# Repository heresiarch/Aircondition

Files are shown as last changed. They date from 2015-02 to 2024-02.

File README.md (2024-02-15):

# Aircondition
A Project using TX21IT+ wireless 868Mhz sensors with RFM12 and PIC24F to control air ventilators based on absolute humidity.
You will find the whole C source and Eagle project files inside.
The Circuit and Software uses the following technologies:
* OW protocoll managing config data for DS2430A 1 wire 256 EEPROM
* Microchip MCU PIC24F P24FJ32GB002
* Hope RFM12B IRQ driven communication with TX21IT+ LaCrosse IT+ Weather sensors
* IC2 communication with Newhaven LCD Display NHD-C0216CiZ-FN-FBW-3V (which was tricky)
* Rotary encoder using digital filter algorithm for debouncing for configuring the system  

The setup is very simple:  
0. The system checks for valid config and CRC in the EEPROM and if OK goes to 3 or step 1  
1. You have to register the 2 TX21IT+ sensors each time you change their battery the get a new ID.  
2. Then you setup in sensor, out sensor, absolute humidity threshold, pause time, run time for ventitalors which is stored in the OW EEPROM  
3. Then the mainloop starts  
3.1. In the Mainlopp the MCU will listen with the RFM12B for 30 TX21IT+ records  
3.2. The ID of the records is used to match in and out sensors configured in step 1 and 2, if no sensor matches found it starts @1   
3.3 The temperature and relative humidity will be used to calculate absolute humidity for the in and out sensor  
3.5 If abs-hum-in > (threshold + abs-hum-out) the AC ventilators will be switched with an SCR  will run as long the configured runtime in step 2  
3.6. The system waits until the pause time is over and starte @3  
At any time a long press on the rotary knob will start reconfiguring mode step 1  

The system runs rockstable since 10 years in my garage with Marley Silenzio Ventilators.  
Not shown is the snubber circuit using a TVS, X2 capacitor and an high voltage resistor to reduce spikes to protect the SCR.
Bottom ventilator blows air from outside, top ventilator blows air to outside.
No moldy smell and always uses the right time for air condition to prevent mold creation during all seasons.  
The project uses MPLABX and has also a .project Eclipse file which I used to utilize Git Eclipse integration to manage versioning.

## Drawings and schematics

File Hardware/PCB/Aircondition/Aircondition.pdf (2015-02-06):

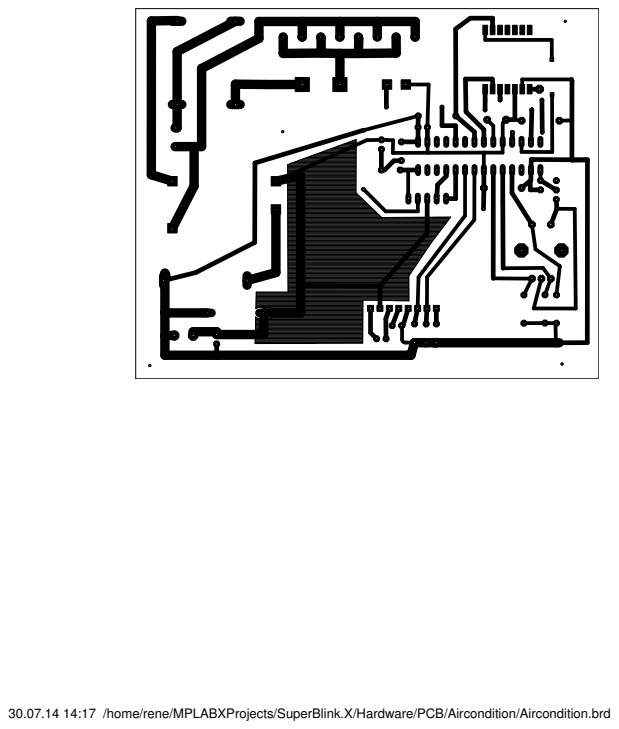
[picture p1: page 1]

30.07.14 14:17 /home/rene/MPLABXProjects/SuperBlink.X/Hardware/PCB/Aircondition/Aircondition.brd

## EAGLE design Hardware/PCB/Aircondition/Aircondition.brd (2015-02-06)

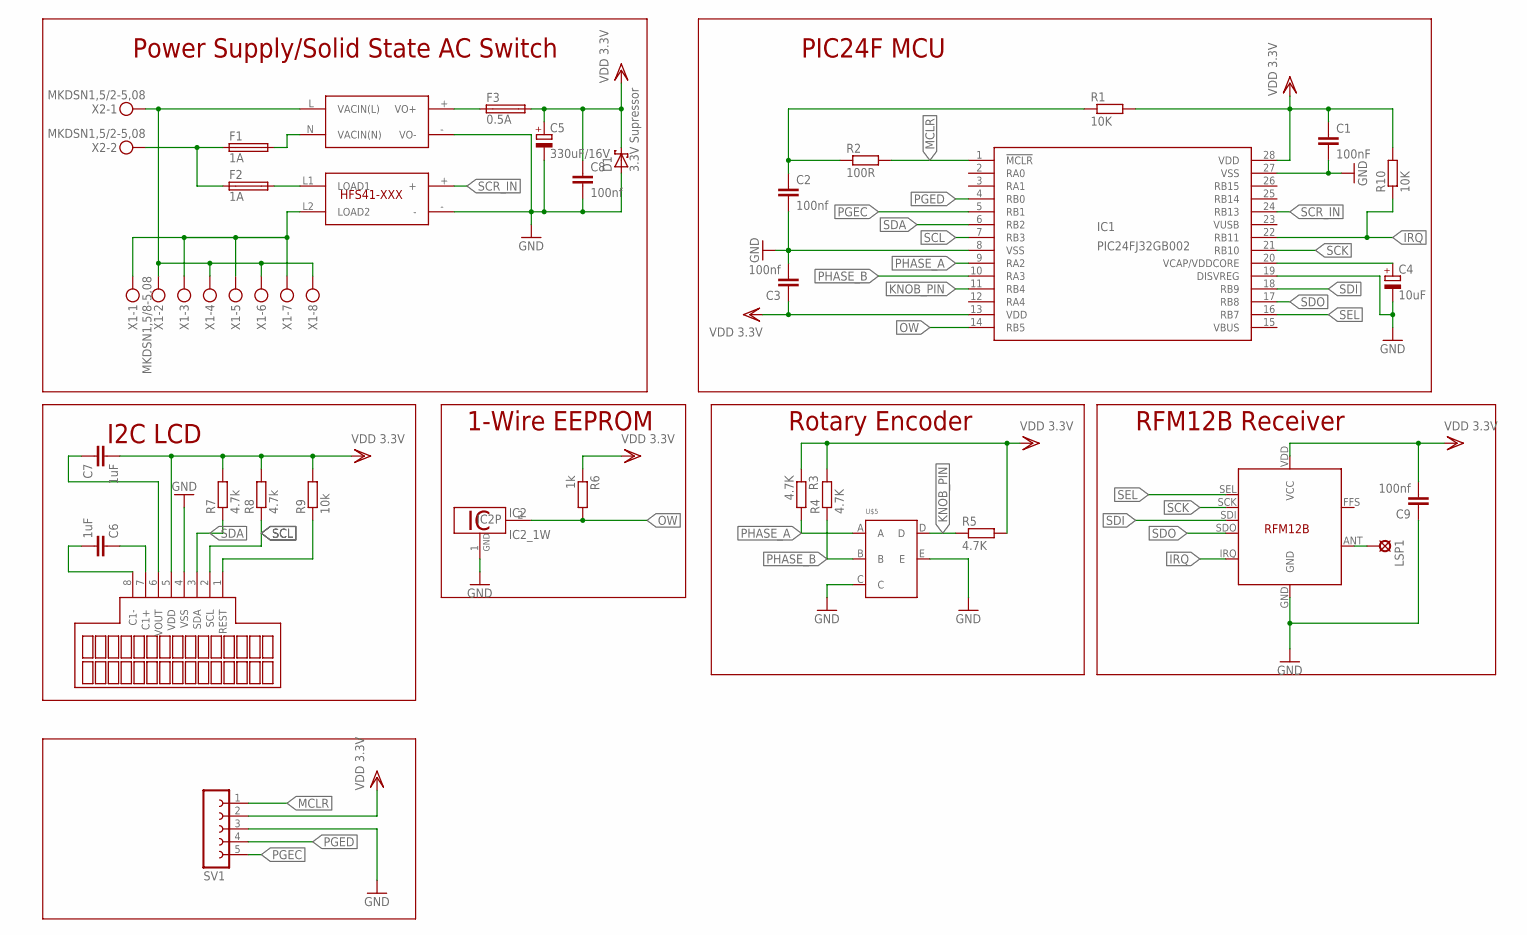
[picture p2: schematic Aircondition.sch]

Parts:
C1: 100nF; C025-025X050
C2, C8: 100nf; C025-025X050
C3, C9: 100nf; C102-043X133
C4: 10uF; E5-5
C5: 330uF/16V; E5-10,5
C6, C7: 1uF; C025-025X050
D1: 3.3V Supressor; C4111-15
F1, F2: 1A; SH22,5A
F3: 0.5A; SH22,5A
IC1: PIC24FJ32GB002; DIL28-3
IC2: DS2431; TO92-
LSP1: ANT; LSP10
R1: 10K; 0204/5
R2: 100R; 0204/5
R3, R4, R5: 4.7K; 0204/7
R6: 1k; 0207/2V
R7, R8: 4.7k; 0204/5
R9: 10k; 0204/5
R10: 10K; 0207/10
SV1: FE05-1
U$1: RAC01-3.3SC; RAC01-XXSC
U$2: HFS41D-240A5Z-NGSTANDARD; HFS41-EXPOXY-RESIN
U$3: NHD-C0216CIZ-FN-FBW-3VSIL8-2.54; SIL8-2.54
U$4: RFM12B
U$5: ENCODER-E; ENCODER
X1: MKDSN1,5/8-5,08
X2: MKDSN1,5/2-5,08

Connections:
GND: C1.2, C2.2, C3.2, C4.-, C5.-, C8.2, C9.1, D1.A, IC1.8 (VSS), IC1.19 (DISVREG), IC1.27 (VSS), IC2.1 (GND), SV1.3, U$1.- (VO-), U$2.-, U$3.4 (VSS), U$4.GND, U$5.C, U$5.E
IRQ: IC1.22 (RB11), R10.1, U$4.IRQ
KNOB_PIN: IC1.11 (RB4), R5.1, U$5.D
MCLR: IC1.1 (!MCLR), R2.2, SV1.1
unnamed: F1.2, U$1.N (VACIN(N))
unnamed: F2.2, U$2.L1 (LOAD1)
unnamed: F1.1, F2.1, X2.2
unnamed: U$2.L2 (LOAD2), X1.1, X1.3, X1.5, X1.7
unnamed: C2.1, R1.1, R2.1
unnamed: U$1.L (VACIN(L)), X1.2, X1.4, X1.6, X1.8, X2.1
unnamed: F3.1, U$1.+ (VO+)
unnamed: C4.+, IC1.20 (VCAP/VDDCORE)
unnamed: LSP1.MP, U$4.ANT
unnamed: C6.2, U$3.8 (C1-)
unnamed: C6.1, U$3.7 (C1+)
unnamed: C7.1, U$3.6 (VOUT)
unnamed: R9.1, U$3.1 (REST)
OW: IC1.14 (RB5), IC2.2 (1W), R6.2
PGEC: IC1.5 (RB1), SV1.5
PGED: IC1.4 (RB0), SV1.4
PHASE_A: IC1.9 (RA2), R3.2, U$5.A
PHASE_B: IC1.10 (RA3), R4.1, U$5.B
SCK: IC1.21 (RB10), U$4.SCK
SCL: IC1.7 (RB3), R8.1, U$3.2 (SCL)
SCR_IN: IC1.24 (RB13), U$2.+
SDA: IC1.6 (RB2), R7.1, U$3.3 (SDA)
SDI: IC1.18 (RB9), U$4.SDI
SDO: IC1.17 (RB8), U$4.SDO
SEL: IC1.16 (RB7), U$4.SEL
VDD: C1.1, C3.1, C5.+, C7.2, C8.1, C9.2, D1.C, F3.2, IC1.13 (VDD), IC1.28 (VDD), R1.2, R3.1, R4.2, R5.2, R6.1, R7.2, R8.2, R9.2, R10.2, SV1.2, U$3.5 (VDD), U$4.VDD (VCC)

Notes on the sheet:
Power Supply/Solid State AC Switch
I2C LCD
1-Wire EEPROM
Rotary Encoder
PIC24F MCU
RFM12B Receiver

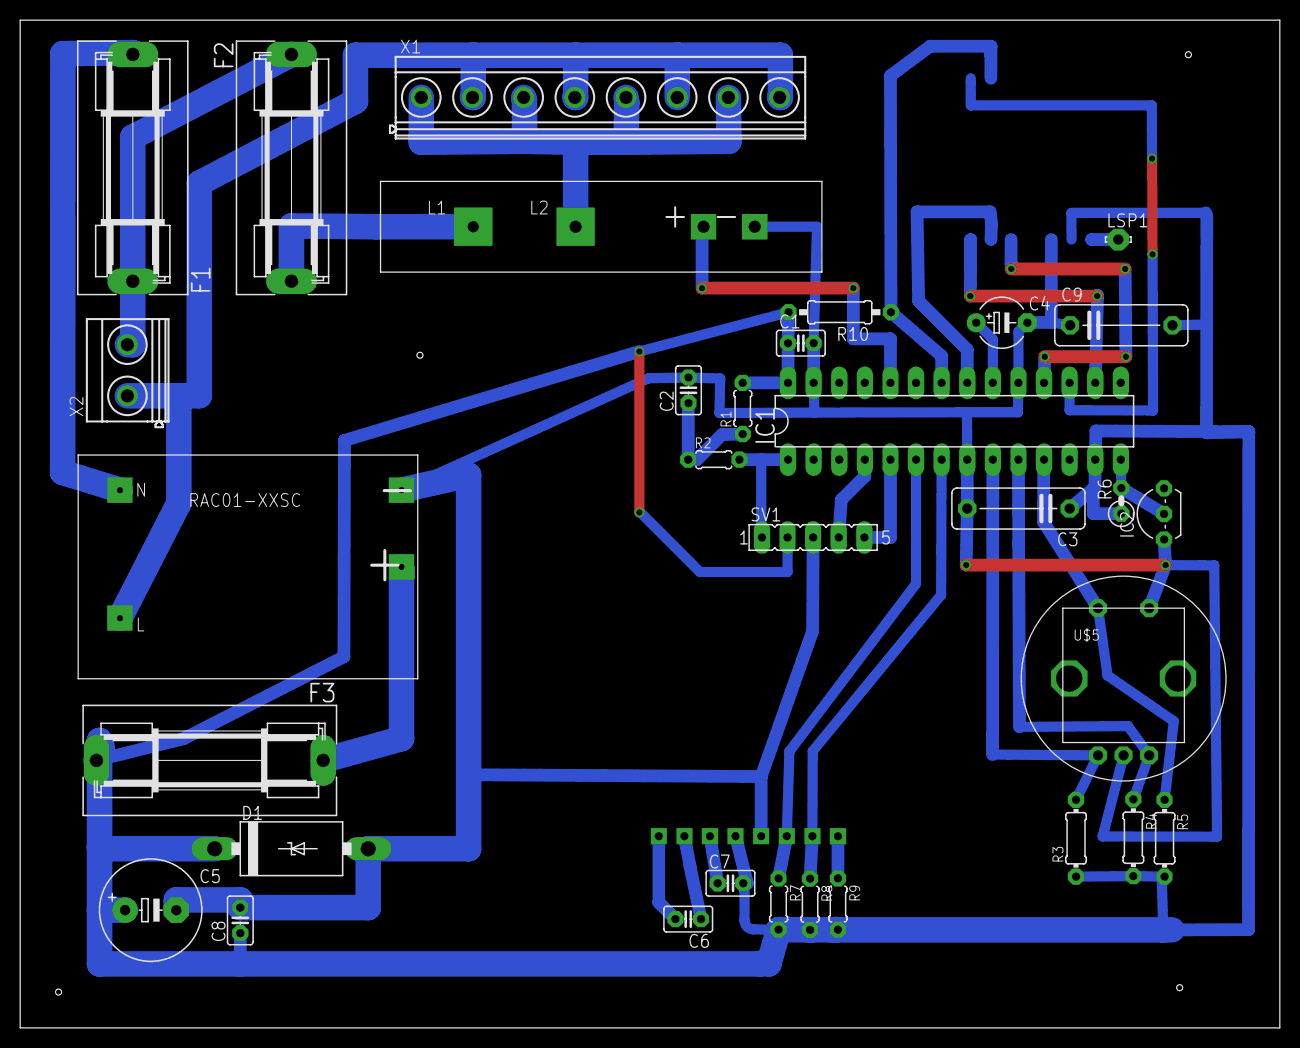
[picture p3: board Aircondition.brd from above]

Board: 2 copper layers, 125.0 x 100.0 mm, 34 parts (1 on the bottom side), 30 nets.

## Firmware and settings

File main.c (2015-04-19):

/* 
 * File:   main.c
 * Author: rene
 *
 * Created on 18. August 2013, 12:57
 */


#include <string.h>
#include <stdint.h>
#include <xc.h>
//#include <p24FJ32GB002.h>
#define FCY 8000000UL
#include <libpic30.h>
#include "LCD_I2C_ST7032i.h"
#include "RFM12B.h"
#include "TX21IT.h"
#include "LCD_I2C_ST7032i.h"
#include "1wire.h"
#include "rotary_encoder.h"
#include "stringconversion.h"
#include "aircondition.h"

/*
// http://www.microchip.com/forums/tm.aspx?m=491233
_CONFIG1(JTAGEN_OFF & GCP_OFF & GWRP_OFF & ICS_PGx1 & FWDTEN_OFF & WINDIS_OFF & FWPSA_PR32 & WDTPS_PS8192);
_CONFIG2(IESO_OFF & FNOSC_FRCPLL & OSCIOFNC_ON & POSCMOD_NONE & PLL96MHZ_ON & PLLDIV_DIV2 & FCKSM_CSDCMD & IOL1WAY_OFF);
_CONFIG3(WPFP_WPFP0 & SOSCSEL_IO & WUTSEL_FST & WPDIS_WPDIS & WPCFG_WPCFGDIS & WPEND_WPENDMEM)
_CONFIG4(DSWDTPS_DSWDTPS3 & DSWDTOSC_LPRC & RTCOSC_LPRC & DSBOREN_OFF & DSWDTEN_OFF)
*/


// CONFIG4
#pragma config DSWDTPS = DSWDTPS3       // DSWDT Postscale Select (1:128 (132 ms))
#pragma config DSWDTOSC = LPRC          // Deep Sleep Watchdog Timer Oscillator Select (DSWDT uses Low Power RC Oscillator (LPRC))
#pragma config RTCOSC = LPRC            // RTCC Reference Oscillator Select (RTCC uses Low Power RC Oscillator (LPRC))
#pragma config DSBOREN = OFF            // Deep Sleep BOR Enable bit (BOR disabled in Deep Sleep)
#pragma config DSWDTEN = OFF            // Deep Sleep Watchdog Timer (DSWDT disabled)

// CONFIG3
#pragma config WPFP = WPFP0             // Write Protection Flash Page Segment Boundary (Page 0 (0x0))
#pragma config SOSCSEL = IO             // Secondary Oscillator Pin Mode Select (SOSC pins have digital I/O functions (RA4, RB4))
#pragma config WUTSEL = FST             // Voltage Regulator Wake-up Time Select (Fast regulator start-up time used)
#pragma config WPDIS = WPDIS            // Segment Write Protection Disable (Segmented code protection disabled)
#pragma config WPCFG = WPCFGDIS         // Write Protect Configuration Page Select (Last page and Flash Configuration words are unprotected)
#pragma config WPEND = WPENDMEM         // Segment Write Protection End Page Select (Write Protect from WPFP to the last page of memory)

// CONFIG2
#pragma config POSCMOD = NONE           // Primary Oscillator Select (Primary Oscillator disabled)
#pragma config I2C1SEL = PRI            // I2C1 Pin Select bit (Use default SCL1/SDA1 pins for I2C1 )
#pragma config IOL1WAY = OFF            // IOLOCK One-Way Set Enable (The IOLOCK bit can be set and cleared using the unlock sequence)
#pragma config OSCIOFNC = ON            // OSCO Pin Configuration (OSCO pin functions as port I/O (RA3))
#pragma config FCKSM = CSDCMD           // Clock Switching and Fail-Safe Clock Monitor (Sw Disabled, Mon Disabled)
#pragma config FNOSC = FRCPLL           // Initial Oscillator Select (Fast RC Oscillator with Postscaler and PLL module (FRCPLL))
#pragma config PLL96MHZ = ON            // 96MHz PLL Startup Select (96 MHz PLL Startup is enabled automatically on start-up)
#pragma config PLLDIV = DIV2            // USB 96 MHz PLL Prescaler Select (Oscillator input divided by 2 (8 MHz input))
#pragma config IESO = OFF               // Internal External Switchover (IESO mode (Two-Speed Start-up) disabled)

// CONFIG1
#pragma config WDTPS = PS8192           // Watchdog Timer Postscaler (1:8,192)
#pragma config FWPSA = PR32             // WDT Prescaler (Prescaler ratio of 1:32)
#pragma config WINDIS = OFF             // Windowed WDT (Standard Watchdog Timer enabled,(Windowed-mode is disabled))
#pragma config FWDTEN = OFF             // Watchdog Timer (Watchdog Timer is disabled)
#pragma config ICS = PGx1               // Emulator Pin Placement Select bits (Emulator functions are shared with PGEC1/PGED1)
#pragma config GWRP = OFF               // General Segment Write Protect (Writes to program memory are allowed)
#pragma config GCP = OFF                // General Segment Code Protect (Code protection is disabled)
#pragma config JTAGEN = OFF             // JTAG Port Enable (JTAG port is disabled)


#define OUTPUTBUFSIZE 16
char outbuf1[OUTPUTBUFSIZE];
char outbuf2[OUTPUTBUFSIZE];
#define RECEIVEBUFSIZE 5
char receiveBuff[RECEIVEBUFSIZE];

volatile uint8_t byteCount = 0;

#define RELAIS_OUT_PIN LATBbits.LATB13
#define RELAIS_OUT_DIR TRISBbits.TRISB13

#define GLOBAL_BUFFER_ELEMENTS 30
TX21SensorData global_buffer[GLOBAL_BUFFER_ELEMENTS];
volatile uint16_t global_counter = 0;


enum Status
{
	CHECK_CONFIG = 1, SET_CONFIG, RUN, ERROR
};

typedef enum Status StatusEnum;
StatusEnum s = CHECK_CONFIG;
StatusEnum old = ERROR;
volatile char dirty = 0;

AirConfigData configData = {0};

// functions for state machine
void state_check_config(void);
void state_set_config(void);
void state_run(void);

int findSensors(void);
uint8_t chooseSensorID(char* msg, TX21SensorData* outArray, uint8_t size);
int16_t chooseIntVal(char* msg, int16_t min, int16_t max, int16_t step);
float chooseFloatVal(char* msg, float min, float max, float step,float precision);


void enableRFM12(void);
void resetRFM12(void);

void Timer1Init(void);

int main(int argc, char** argv) {

    global_counter = 0;

    CLKDIVbits.PLLEN       = 1;     //PLL enable
    while(OSCCONbits.LOCK!=1) {};   //wait for stable PLL
    __delay_ms(5000);

    AD1PCFGL = 0xFFFF;      // all Ports digital
    TRISBbits.TRISB15 = 0;
    TRISBbits.TRISB14 = 0;
    TRISBbits.TRISB13 = 0;
    //RESET Line of RFM12b
    TRISBbits.TRISB11 = 1;
    //KNOB_PIN
    TRISBbits.TRISB4 = 1;
    //Rotary Phases
    TRISAbits.TRISA2 = 1;
    TRISAbits.TRISA4 = 1;

    RPINR0	=	0x0B00;	//set RP11 to external interrupt 1
    INTCON2 = 0xFFFF;   /*Setup INT0, INT1, INT2, interupt on falling edge*/
    IFS1bits.INT1IF = 0;    /*Reset INT1 interrupt flag */
    IEC1bits.INT1IE = 1;    /*Enable INT1 Interrupt Service Routine */
    IPC5bits.INT1IP = 5;	/*set low priority*/

    //RELAIS
    RELAIS_OUT_DIR = 0;
    RELAIS_OUT_PIN = 0;
    Timer1Init();
    lcd2_init();
    encode_init();
    s = SET_CONFIG;
    old = ERROR;
    lcd2_clear();
    lcd2_home();
    lcd2_write_str_xy(0,0,"Aircondition");
    lcd2_write_str_xy(0,1,"Rene Meyer 2014");
    __delay_ms(5000);
    s = CHECK_CONFIG;
    while(1)
    {
        // State changed
	if(old != s)
	{
            lcd2_clear();
            lcd2_home();
            old = s;
            dirty = 1;	
	}
        switch (s)
	{
		case CHECK_CONFIG:
			state_check_config();
		break;
                case SET_CONFIG:
			state_set_config();
		break;
                case RUN:
                        state_run();
		break;
                case ERROR:
			state_set_config();
		break;
	}

    }

    return 0;
}

void state_check_config(void)
{
    // first read configdata
    uint8_t len = sizeof(AirConfigData);
    read_ds2430(6, (uint8_t*)&configData, len);
    // read crc
    uint8_t crc = 0;
    read_ds2430(6+len, (uint8_t*)&crc, sizeof(uint8_t));
    uint8_t realcrc = crc8((uint8_t*)&configData,len);
    lcd2_clear();
    lcd2_home();
    if(crc != realcrc)
    {
        lcd2_write_str_xy(0,0,"Invalid Config");
        lcd2_write_str_xy(0,1,"Press Knob");
        while(!knob_up());
        s = SET_CONFIG;
    }
    else
    {
        lcd2_write_str_xy(0,0,"Config OK");
        __delay_ms(1000);
        s = RUN;
    }
}

void state_set_config(void)
{
    uint16_t found = findSensors();
    if(found == 0)
    {
        lcd2_clear();
        lcd2_home();
        lcd2_write_str_xy(0,0,"No Sensors found!");
        lcd2_write_str_xy(0,1,"Restart Config");
        while(!knob_up());
        s = CHECK_CONFIG;
    }
    else
    {
        configData.inSensorID = chooseSensorID("Choose In Sensor", global_buffer, found);
        configData.outSensorID = chooseSensorID("Choose Out Sensor", global_buffer, found);
        configData.runTime = chooseIntVal("Runtime min",MIN_RUN_MINUTES,MAX_RUN_MINUTES,RUN_STEP);
        configData.pauseTime = chooseIntVal("Pause min",MIN_PAUSE_TIME_MINUTES, MAX_PAUSE_TIME_MINUTES,PAUSE_TIME_MINUTES_STEP);
        configData.breakAfterRunTime = chooseIntVal("Break min", MIN_BREAK_BTW_RUNS_MINUTES, MAX_BREAK_BTW_RUNS_MINUTES,BREAK_BTW_RUNS_MINUTES_STEP);
        configData.threshold = chooseFloatVal("Ta Thresh. g/m^3",MIN_ABS_HUMIDITY_THRESHOLD, MAX_ABS_HUMIDITY_THRESHOLD, ABS_HUMIDITY_STEP,ABS_HUMIDITY_PRECISION);
        //Write Config to EEPROM
        uint8_t len = sizeof(AirConfigData);
        uint8_t buf[len];
        memcpy(buf,&configData,len);
        write_ds2430(6, buf, len);
        //write crc to EEPROM
        uint8_t crc = crc8((uint8_t*)&configData,len);
        uint8_t buf2[2];
        buf2[0]=crc;
        buf2[1]=0;
        write_ds2430(6+len, buf2, sizeof(uint8_t));
        lcd2_clear();
        lcd2_home();
        lcd2_write_str_xy(0,0,"Config. written");
        lcd2_write_str_xy(0,1,"Press Knob ");
        while(!knob_up());
        s = CHECK_CONFIG;
    }

}

void state_run(void)
{
    TX21SensorData inData;
    TX21SensorData outData;
    while(s == RUN)
    {
        char out = 0;
        int pause_counter = 0;
        int break_counter = 0;
        int out_counter = 0;
        int found = findSensors();
        if(found <= 0)
        {
            lcd2_clear();
            lcd2_home();
            lcd2_write_str_xy(0,0,"Error:");
            lcd2_write_str_xy(0,0,"No Sensors!");
            while(!knob_up());
            s = ERROR;    
            return;
        }
        int inIdx = -1;
        int outIdx = -1;
        int i;
        for(i = 0; i < found; i++)
        {
            if(global_buffer[i].sensorID == configData.inSensorID)
            {
                inIdx = i;
            }
            else if(global_buffer[i].sensorID == configData.outSensorID)
            {
                outIdx = i;
            }
        }
        if(inIdx < 0 || outIdx < 0)
        {
            lcd2_clear();
            lcd2_home();
            lcd2_write_str_xy(0,0,"Error:");
            lcd2_write_str_xy(0,1,"No ID Match!");
            while(!knob_up());
            s = ERROR;
            return;
        }
        inData = global_buffer[inIdx];
        outData = global_buffer[outIdx];
        float absHumIn = getAbsoluteHumidity(&inData);
        float absHumOut = getAbsoluteHumidity(&outData);
        float comp = absHumOut + configData.threshold;
        if(comp < absHumIn)
        {
            out = 1;
            RELAIS_OUT_PIN = 1;
        }
        else
        {
            out = 0;
            RELAIS_OUT_PIN = 0;
        }
        //loop for Running Aircondition
        while((out_counter < configData.runTime * 60) && out && s == RUN)
        {
            char battbuff[8];
            lcd2_clear();
            lcd2_home();
            lcd2_write_str_xy(0,0,"Air Condition");
            lcd2_write_str_xy(0,1,"Run ");
            int secsLeft = (configData.runTime * 60 - out_counter);
            lcd2_write_U16(secsLeft,0);
            lcd2_write_str(" sec");
            __delay_ms(2000);
            lcd2_clear();
            lcd2_home();
            lcd2_write_str("In:");
            lcd2_write_U8_hex(inData.sensorID);
            lcd2_write_str(" ");
            getSensorBatteryStateString(battbuff,sizeof(battbuff),&inData);
            lcd2_write_str(battbuff);
            getSensorValueString(outbuf1,OUTPUTBUFSIZE, &inData);
            lcd2_write_str_xy(0,1,outbuf1);
            __delay_ms(2000);
            lcd2_clear();
            lcd2_home();
            lcd2_write_str("Out:");
            lcd2_write_U8_hex(outData.sensorID);
            lcd2_write_str(" ");
            getSensorBatteryStateString(battbuff,sizeof(battbuff),&outData);
            lcd2_write_str(battbuff);
            getSensorValueString(outbuf1,OUTPUTBUFSIZE, &outData);
            lcd2_write_str_xy(0,1,outbuf1);
            __delay_ms(2000);
            out_counter+=6;
            if(long_pressed())
            {
                s = ERROR;
            }
        }
        // special wait after run
        if(out == 1)
        {
            out = 0;
            RELAIS_OUT_PIN = 0;
            while(break_counter < configData.breakAfterRunTime * 60)
            {
                lcd2_clear();
                lcd2_home();
                lcd2_write_str_xy(0,0,"Air Condition");
                lcd2_write_str_xy(0,1,"Break after Run ");
                int secsLeft = (configData.breakAfterRunTime * 60 - break_counter);
                lcd2_write_U16(secsLeft,0);
                lcd2_write_str(" sec");
                __delay_ms(1000);
                break_counter += 1;
                if(long_pressed())
                {
                    s = ERROR;
                }
            }
        }
        
        while(pause_counter < configData.pauseTime * 60 && s == RUN)
        {
            lcd2_clear();
            lcd2_home();
            lcd2_write_str_xy(0,0,"Air Condition");
            lcd2_write_str_xy(0,1,"Pause ");
            int secsLeft = (configData.pauseTime * 60 - pause_counter);
            lcd2_write_U16(secsLeft,0);
            lcd2_write_str(" sec");
            __delay_ms(1000);
            pause_counter += 1;
            if(long_pressed())
            {
                s = ERROR;
            }
        }
    }
}


int findSensors()
{
    global_counter = 0;
    lcd2_clear();
    lcd2_home();
    lcd2_write_str_xy(0,0,"Search TX21IT+");
    lcd2_write_str_xy(0,1,"Sensors");
    __delay_ms(1000);
    uint16_t counter = 0;
    uint16_t found = 0;
    char battbuff[8];
    while(counter < 50 && global_counter < GLOBAL_BUFFER_ELEMENTS)
    {
       enableRFM12();
       __delay_ms(1500);
       lcd2_clear();
       lcd2_home();
       lcd2_write_str("...");
       lcd2_write_U8(global_counter,0);
       lcd2_write_str(" Records");
       __delay_ms(500);
       counter++;
       resetRFM12();
       volatile uint16_t idx = global_counter;
       if(idx > 0)
       {
           TX21SensorData data = global_buffer[idx-1];
           lcd2_clear();
           lcd2_home();
           lcd2_write_U8_hex(data.sensorID);
           lcd2_write_str(" ");
           getSensorBatteryStateString(battbuff,sizeof(battbuff), &data);
           lcd2_write_str(battbuff);
           getSensorValueString(outbuf1,OUTPUTBUFSIZE, &data);
           lcd2_write_str_xy(0,1,outbuf1);
        __delay_ms(500);
       }
    }
    found = global_counter;
    return found;
}

uint8_t chooseSensorID(char* msg, TX21SensorData* outArray, uint8_t size)
{
    uint8_t ret = 0;
    lcd2_clear();
    lcd2_home();
    lcd2_write_str_xy(0,0,msg);
    lcd2_write_str_xy(0,1,"Rotate/press knob");
    while(!knob_up());
    int8_t idx = 0;
    int8_t old_idx = -1;
    TX21SensorData data;
    while(1)
    {
        char delta = encode_read4();
        if(delta < 0 && idx > 0)
        {
            idx--;
        }
        else if(delta > 0 && idx < (size-1))
        {
            idx++;
        }
        if(old_idx != idx)
        {
            old_idx = idx;
            lcd2_clear();
            lcd2_home();
            lcd2_write_U8_hex(outArray[idx].sensorID);
            data = outArray[idx];
            getSensorValueString(outbuf1,OUTPUTBUFSIZE, &data);
            lcd2_write_str_xy(0,1,outbuf1);
        }
        if(knob_up())
        {
            ret = outArray[idx].sensorID;
            break;
        }
     }
    return ret;
}

int16_t chooseIntVal(char* msg, int16_t min, int16_t max, int16_t step)
{
    char ret = -1;
    lcd2_clear();
    lcd2_home();
    int16_t idx = min;
    int16_t old_idx = -1;
    while(1)
    {
        char delta = encode_read4();
        if(delta < 0 && idx >= (min + step))
        {
            idx-=step;
        }
        else if(delta > 0 && idx <= (max-step))
        {
            idx+=step;
        }
        if(old_idx != idx)
        {
            old_idx = idx;
            lcd2_clear();
            lcd2_home();
            lcd2_write_str(msg);
            lcd2_goto_xy(0,1);
            lcd2_write_U16(idx,0);

        }
        if(knob_up())
        {
            ret = idx;
            break;
        }
     }
    return ret;
}

float chooseFloatVal(char* msg, float min, float max, float step,float precision)
{
    float ret = 0.0;
    lcd2_clear();
    lcd2_home();
    float idx = min;
    float old_idx = -1.0;
    while(1)
    {
        char delta = encode_read4();
        if(delta < 0 && idx >= (min + step))
        {
            idx-=step;
        }
        else if(delta > 0 && idx <= (max-step))
        {
            idx+=step;
        }
        if(old_idx != idx)
        {
            old_idx = idx;
            lcd2_clear();
            lcd2_home();
            lcd2_write_str(msg);
            //ftoa(floatbuf,idx,precision);
            char* floatbuf = sc_float_to_str(idx,precision);
            lcd2_goto_xy(0,1);
            lcd2_write_str(floatbuf);
        }
        if(knob_up())
        {
            ret = idx;
            break;
        }
     }
    return ret;
}

void enableRFM12(void)
{
    RFM12B_PORT_INIT();
    RFM12B_INIT(0);

    /*
     RFM12B_CMD(0xCA80); // enable sensitive reset (required for software reset)
     RFM12B_CMD(0xFE00); // software reset command
     __delay_ms(100); // give RFM time to do software reset (which should only take 0.25ms)
    RFM12B_CMD(0xCA81); // disable sensitive reset

     */
    RFM12B_CMD(0x0000);
    RFM12B_CMD(0x0000);
    RFM12B_CMD(0x82C8); // Init Receiver
    RFM12B_CMD(0xCA81); // Enable FIFO
    RFM12B_CMD(0xCA83); // Clear FIFO
    byteCount=0;
}

void resetRFM12(void)
{
    __asm__ volatile("disi #0x3FFF");
    RFM12B_CMD(0xff00);
     byteCount=0;
    __delay_ms(50);
    __asm__ volatile("disi #0x0000");
}



//_INT1Interrupt() is the INT1 interrupt service routine (ISR).
void __attribute__((__interrupt__)) _INT1Interrupt(void);
void __attribute__((__interrupt__, auto_psv)) _INT1Interrupt(void)
{
    RFM12B_CMD(0x0000);
    char byte = RFM12B_CMD(0xB000);
    if(byteCount!=RECEIVEBUFSIZE)
    {
        receiveBuff[byteCount] = byte;
        byteCount++;
    }
    else
    {
        byteCount = 0;
        RFM12B_CMD(0xCA81);
        RFM12B_CMD(0xCA83);
        TX21SensorData data;
        if(decodeITPlusFrame((unsigned char*) receiveBuff,&data) && global_counter < GLOBAL_BUFFER_ELEMENTS)
        {
            global_buffer[global_counter] = data;
            global_counter++;
        }
    }
   IFS1bits.INT1IF = 0;    //Clear the INT1 interrupt flag or else
   //the CPU will keep vectoring back to the ISR
}


// 1000Hz
void Timer1Init(void)
{
   PR1 = 8000;
   IPC0bits.T1IP = 1;	 //set interrupt priority
   T1CON = 0x8000;	//turn on the timer prescaler 256
   IFS0bits.T1IF = 0;	 //reset interrupt flag
   IEC0bits.T1IE = 1;	 //turn on the timer1 interrupt
}

//_T1Interrupt() is the T1 interrupt service routine (ISR).
void __attribute__((__interrupt__)) _T1Interrupt(void);
void __attribute__((__interrupt__, auto_psv)) _T1Interrupt(void)
{
   //RELAIS_OUT_PIN =~ RELAIS_OUT_PIN;	//Toggle output to LED
   rotarydecode();
   debounce_switch();
   IFS0bits.T1IF = 0;
}

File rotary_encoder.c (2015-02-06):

#include "rotary_encoder.h"
#include "rotary_encoder_customization.h"

volatile int8_t enc_delta;          // -128 ... 127
static int8_t last;
uint8_t y_old = 0;
uint8_t flag = 0;
uint16_t  long_counter = 0;
knob_state knob ={0};


void encode_init( void )
{
  int8_t new;
  new = 0;
  if( PHASE_A )
    new = 3;
  if( PHASE_B )
    new ^= 1;                   // convert gray to binary
  last = new;                   // power on state
  enc_delta = 0;
  knob.knob_up = 0;
  knob.long_pressed = 0;
}

void rotarydecode(void)
{
  int8_t new, diff;
  new = 0;
  if( PHASE_A )
    new = 3;
  if( PHASE_B )
    new ^= 1;                   // convert gray to binary
  diff = last - new;                // difference last - new
  if( diff & 1 ){               // bit 0 = value (1)
    last = new;                 // store new as next last
    enc_delta += (diff & 2) - 1;        // bit 1 = direction (+/-)
  }
}


int8_t encode_read1( void )         // read single step encoders
{
  int8_t val;
  val = enc_delta;
  enc_delta = 0;
  return val;                   // counts since last call
}

int8_t encode_read2( void )         // read two step encoders
{
  int8_t val;
  val = enc_delta;
  enc_delta = val & 1;
  return val >> 1;
}

int8_t encode_read4( void )         // read four step encoders
{
  int8_t val;
  val = enc_delta;
  enc_delta = val & 3;
  return val >> 2;
}

void debounce_switch(void)
{
	uint8_t temp = 0;
	temp=(y_old>>2);
	y_old=y_old-temp;
	if(KNOB_PIN == 0)
	{
		y_old=y_old+0x3F;
	}
	if((y_old > 0xF0)&&(flag==0))
	{
		flag=1;
		knob.long_pressed = 0;
		long_counter = 0;
	}
	if((y_old < 0x0F)&&(flag==1))
	{
		if(knob.long_pressed== 0)
		{
			knob.knob_up = 1;
		}
		flag=0;
		knob.long_pressed = 0;
		long_counter = 0;
	}
	if( flag == 1)
	{
		long_counter++;
	}
	else
	{
		long_counter = 0;
	}

	if(long_counter > 1024)
	{
		knob.long_pressed = 1;
	}
}

knob_state* get_knob_state()
{
    return &knob;
}

uint8_t knob_up(void)
{
    uint8_t ret = knob.knob_up;
    //clear state
    knob.knob_up = 0;
    return ret;
}

uint8_t long_pressed(void)
{
    uint8_t ret = 0;
    if(knob.long_pressed > 0)
    {
        knob.long_pressed = 0;
        ret = 1;
    }
    return ret;
}




/*
int main( void )
{
  int32_t val = 0;

  LEDS_DDR = 0xFF;
  encode_init();
  sei();

  for(;;){
    val += encode_read1();          // read a single step encoder
    LEDS = val;
  }
}*/

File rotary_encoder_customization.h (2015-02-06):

/* 
 * File:   rotary_encoder_customization.h
 * Author: rene
 *
 * Created on 24. Mai 2014, 09:57
 */

#ifndef ROTARY_ENCODER_CUSTOMIZATION_H
#define	ROTARY_ENCODER_CUSTOMIZATION_H
#include <xc.h>
#define FCY 8000000UL
#include <libpic30.h>
//Rotary Encoder PIN Definitions
#define PHASE_B  PORTAbits.RA2
#define PHASE_A  PORTAbits.RA3
#define KNOB_PIN PORTBbits.RB4

#endif	/* ROTARY_ENCODER_CUSTOMIZATION_H */
